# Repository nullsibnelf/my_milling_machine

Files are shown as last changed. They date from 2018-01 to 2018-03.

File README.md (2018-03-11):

# my_milling_machine
open source hardware - PCB-milling and engraving machine

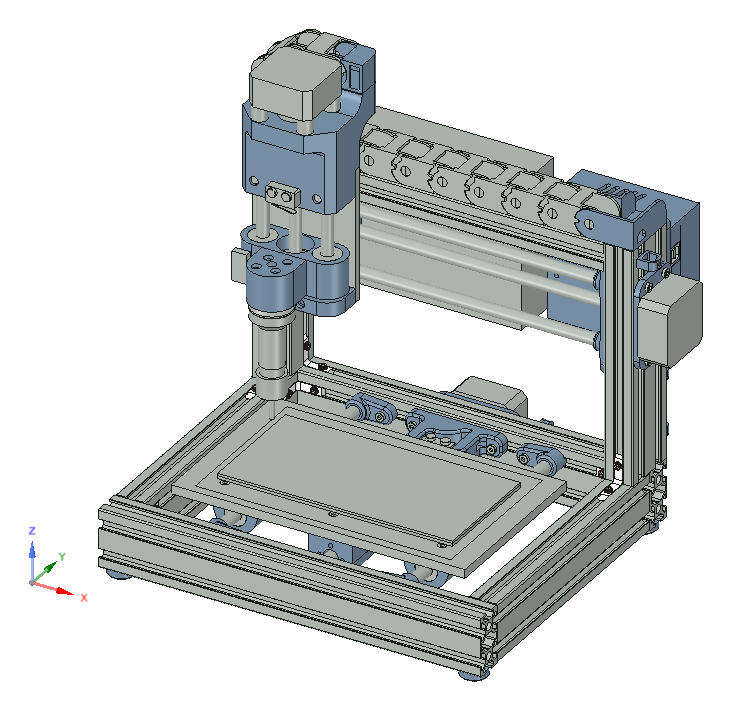
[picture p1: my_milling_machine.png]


Goal:
- low budget machine to make pcb's without expensive software
- little machine overall size, to fit in a cupboard
- open hardware to support further development

<p>&nbsp;</p>

Features:
- Size 310 x 260 x 280 mm
- working volume 173 x 108 x 35 mm
- standard 1/8" tool fitting
- Arduino based
- connection via USB or Bluetooth
- auto-homing

<p>&nbsp;</p>

Further Development:
- Tool referencing
- interchangeable toolhead for mounting a laser module too
- camera for optical calibration
- dust extraction [Link](https://github.com/nullsibnelf/cyclone_dust_absorber)
- emergency shutdown

<p>&nbsp;</p>

2018/02/26: Total costs by now -> ~237€ plus 3D-printed parts

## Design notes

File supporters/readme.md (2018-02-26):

This section is for all those they supported this project with ideas, work and goods.    

**Special Thanks to:**

<br><p>
  
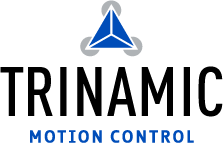
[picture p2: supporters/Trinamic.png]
    
  
**Trinamic**, for free testsamples of the <a href="https://www.trinamic.com/products/integrated-circuits/details/tmc2130/" target="_blank">TMC2130</a> for evaluation of my Arduino-CNC-HAT!    
Really great chip!    

<br><p>
  
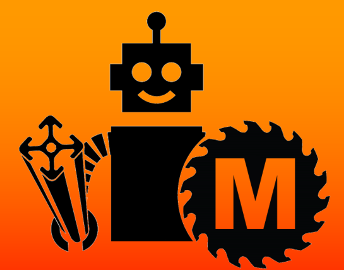
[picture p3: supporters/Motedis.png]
    
  
**Motedis**, for their great support and patience in mechanical qustions about the frame.    
Cheap parts at accurate and high quality! Get yours <a href="http://www.motedis.com/shop/">here!</a>

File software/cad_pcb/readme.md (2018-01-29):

folder for cad-files and the software Eagle from CADSoft.

<br>
<i>Eagle:</i>

All pcb-cad-files are made with Eagle.    
Download: http://ftp.cadsoft.de/freeware.htm
<p>&nbsp;<br></p>

<br>
<i>ULP Script pcb-gcode:</i>

To make gcode out of your board-file you need this ULP-script.    
Download: http://pcbgcode.org/list.php?12   

Changes: in file "settings/gcode-defaults.h" line 49 change    
```string SPINDLE_ON = "M03" + EOL + DWELL;```    
into    
```string SPINDLE_ON = "M03 S20" + EOL + DWELL;```

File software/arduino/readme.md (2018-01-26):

folder for arduino codes.
<p>&nbsp;</p>

<p>
<b>HC-05_config.ino:</b><br>    
This Sketch helps to configure the bluetooth module. You have to change the name, password and baudrate.<br>
Instruction how to do this can be found here: http://www.instructables.com/id/Modify-The-HC-05-Bluetooth-Module-Defaults-Using-A/
</p>
<p>&nbsp;</p>

<p>
<b>ESC_test.ino:</b><br>        
This Sketch was to test the ESC to run a brushless motor controlled by the arduino. Just for evaluation. Not needed.
</p>
<p>&nbsp;</p>

<p>
<b>GRBL:</b><br>     
My-milling-machine runs with GRBL firmware. It's a open source arduino based software that controlls the whole machine.<br>
Download: https://github.com/gnea/grbl/releases
</p>
<p>&nbsp;</p>

<p>
<b>GRBL ESC-patch:</b><br>       
My-milling-machine uses a brushless motor instead of an high-revolution cnc-spindle. GRBL doesn't support this by now. But there is a fork working, made by <a href="https://github.com/pablozg" target="new">pablozg</a>. Thanks for that!<br>
Download: https://github.com/gnea/grbl/pull/163/commits/012c7ed89ec174e6f918a2663bce6ed2ce5e7117
</p>
<p>&nbsp;</p>

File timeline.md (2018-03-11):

2018/01/29:    
All metal parts ordered. ETA 2-3 weeks.    

<br>

2018/02/13:    
Frame parts arrived today. Let's build it :-)

<br>

2018/02/22:    
ordered some wrong pieces. updated partlist accordingly. Waiting for the right parts now.

<br>

2018/03/11:    
Führung der Y-Achsen-Führung überarbeitet. Durch shrinking der 3D-Druckteile klemmten die Linearführungen leicht. Halter in 3 Teile gesplittet.    
Motoren für X und Y montiert und getestet. Verdrahtung und GRBL Konfiguration entsprechend angepasst.

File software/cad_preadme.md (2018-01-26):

folder for cad-files and the software Eagle from CADSoft.

<br>
All pcb-cad-files are made with Eagle.
Download: http://ftp.cadsoft.de/freeware.htm

<br>
To make gcode out of your board-file you need this ULP-script.
Download: http://pcbgcode.org/list.php?12

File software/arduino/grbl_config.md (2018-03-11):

Setting | Value | Beschreibung
--- | --- | --- 
$0   | 10 | 
$1   | 25 | 
$2   | 0 | 
$3   | 1 | Motor der X-Achse auf "Max"-Seite montiert
$4   | 0 | 
$5   | 0 | 
$6   | 0 | 
$10  | 1 | 
$11  | 0.010 | 
$12  | 0.002 | 
$13  | 0 | Maße in Millimeter
$20  | 1 | Softlimits aktiviert für Max-Position
$21  | 1 | Endschalter aktiviert für Homing
$22  | 1 | Homing freigeschaltet
$23  | 3 | Homing X + Y nach Null, Z nach Max
$24  | 25.000 | 
$25  | 500.000 | 
$26  | 250 | 
$27  | 2.000 | Verfahrweg für Freigabe der Endschalterin Millimetern
$30  | 1000 | 
$31  | 0 | 
$32  | 0 | 
$100 | 100.000 | Stepps pro Millimeter X-Achse
$101 | 100.000 | Stepps pro Millimeter Y-Achse
$102 | 100.000 | Stepps pro Millimeter Z-Achse
$110 | 500.000 | Max-Verfahrrate mm/min X-Achse
$111 | 500.000 | Max-Verfahrrate mm/min Y-Achse
$112 | 500.000 | Max-Verfahrrate mm/min Z-Achse
$120 | 10.000 | Beschleunigung mm/sec² X-Achse
$121 | 10.000 | Beschleunigung mm/sec² Y-Achse
$122 | 10.000 | Beschleunigung mm/sec² Z-Achse
$130 | 175.000 | Max-Weg X-Achse (173 + 2mm für Endtaster)
$131 | 110.000 | Max-Weg Y-Achse (108 + 2mm für Endtaster)
$132 | 38.000 | Max-Weg Z-Achse (36 + 2mm für Endtaster)

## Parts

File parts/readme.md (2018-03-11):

folder for parts you need to build my_milling_machine
<p>&nbsp;</p>

**Machine parts:**

Part | Price | Link | Tested
--- | --- | --- | ---
Arduino Uno clone | 3,41 € | <a href="https://www.banggood.com/UNO-R3-ATmega328P-Development-Board-For-Arduino-No-Cable-p-964163.html" target="_blank">Link</a> | checked
HC-05 bluetooth module | 3,66 € | <a href="https://www.banggood.com/de/3Pcs-HC-05-Wireless-Bluetooth-Serial-Transceiver-Module-For-Arduino-p-1011725.html" target="_blank">Link</a> | checked
Stepper motor driver (3x) | 32,85 € | <a href="http://www.watterott.com/de/SilentStepStick-TMC2130" target="_blank">Link</a> | checked
ESC for spindle | 15,66 € | <a href="https://www.amazon.de/gp/product/B07661T5N2/ref=oh_aui_detailpage_o00_s02?ie=UTF8&psc=1" target="_blank">Link</a> | checked
Brushless motor | 7,50 € | <a href="https://www.amazon.de/LHI-MT2204%E2%85%A1-Brushless-Quadcopter-Multicopter/dp/B01E3OT7NE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" target="_blank">Link</a> | checked
5mm ER11 spindle | 4,02 € | <a href="https://www.banggood.com/ER11A-5mm-Extension-Rod-Holder-Motor-Shaft-Collet-Chuck-Tool-Holder-CNC-Milling-p-1073852.html" target="_blank">Link</a> | checked
1/8" ER11 clamp | 0,82 € | <a href="https://www.banggood.com/ER11-18-Inch-Spring-Collet-for-CNC-Milling-Lathe-Tool-p-1080679.html" target="_blank">Link</a> | checked
Trapezoidal threaded rod with carrier and bearings (3x) | 38,94 € | <a href="https://www.amazon.de/gp/product/B06Y583KK4/ref=ox_sc_act_title_2?smid=AK9FVUO3F9GPF&psc=1" target="_blank">Link</a> | under investigation
Slide bearing (8x) | 12,00 € | <a href="https://www.amazon.de/gp/product/B06WD7M4ZJ/ref=ox_sc_act_title_3?smid=A2LZ0UUKEAXYKL&psc=1" target="_blank">Link</a> | checked
Power supply 100W 12V & 5V | 10,63 € | <a href="https://www.banggood.com/5V12V24V-Power-Supply-Box-For-large-Game-Consoles-p-1120203.html" target="_blank">Link</a> | under investigation
Nema17 stepper motor short (3x) | 30,99 € | <a href="https://www.amazon.de/Beauty-Star-Schrittmotor-Haltemomentf%C3%BCr-Halterung/dp/B07784Y8ML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" target="_blank">Link</a> | checked
End switch (3x) | 0,59 € | <a href="https://www.amazon.de/gp/product/B00U8MPFLO/ref=oh_aui_search_detailpage?ie=UTF8&psc=1" target="_blank">Link</a> | checked
Supply cable 230V (or equivalent) | tbd | n/a |
wiring cables | tbd | n/a |
PE cables | tbd | n/a |
CNC-shield for Arduino | self made | [Link](https://github.com/nullsibnelf/my_milling_machine/tree/master/parts/arduino_shield) | under redesign
Coolingfan for step-drivers on CNC-shield | tbd | n/a |
Reset / emergency-Stop switch | tbd | n/a |
&nbsp; | 161,07 € | |
<p>&nbsp;</p>

**Frame parts:**

Part | Price | Link | Comment
--- | --- | --- | ---
Profile 20x40 B-Typ Nut 6 | 10,89 € |	<a href="http://www.motedis.com/shop/Nutprofil/20-B-Typ-Nut-6/Aluprofil-20x40-B-Typ-Nut-6::158.html" target="_blank">Link</a>
Precision guide bar 8mm Alu (6x + rest) | 15,23 € |	<a href="http://www.motedis.com/shop/Dynamik-Lineareinheiten/Praezisionswellen/Alu-Praezisionswellen-Zuschnitt/Praezisionswelle-Aluminium-%D88mm::3501.html" target="_blank">Link</a>
Machine table 6mm Alu (200x120) |	6,56 € |	<a href="http://www.motedis.com/shop/Halbzeuge/Aluminium-Plaettchen/Aluminium-Plaettchen-beidseitig-feinstgefraest-und-foliert-Plaettchen-Zuschnitt/Plaettchen-Zuschnitt/Alumi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" target="_blank">Link</a>
Spindle mounting plate 6mm Alu (80x64) |	1,39 € |	<a href="http://www.motedis.com/shop/Halbzeuge/Aluminium-Plaettchen/Aluminium-Plaettchen-beidseitig-feinstgefraest-und-foliert-Plaettchen-Zuschnitt/Plaettchen-Zuschnitt/Alumi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" target="_blank">Link</a>
Energy chain links (12x) |	4,86 € |	<a href="http://www.motedis.com/shop/Energiekette/Energiekette/Energiekette-CK15/Energiekette-CK-15-Breite-15mm-einzelne-Glieder::2948.html" target="_blank">Link</a>
Energy chain tail (2x) |	2,69 € |	<a href="http://www.motedis.com/shop/Energiekette/Energiekette/Energiekette-CK15/Energiekette-CK-15-Breite-15mm-Anschlusselemente-1-Paar::2946.html" target="_blank">Link</a>
Profile Nut M3 (30x) |  	6,72 € | <a href="http://www.motedis.com/shop/Nutprofil-Zubehoer/Zubehoer-20-B-Typ-Nut-6/Hammermutter-B-Typ-Nut-6-M3::4752.html" target="_blank">Link</a>
Profile Joint (16x) | 		14,63 € | <a href="http://www.motedis.com/shop/Nutprofil-Zubehoer/Zubehoer-20-B-Typ-Nut-6/Innenwinkel-Stahl-20-B-Typ-Nut-6-099I90R06::565.html" target="_blank">Link</a>
shipping |	11,90 € |
&nbsp; |	74,87 € |	
 
<p>&nbsp;</p>

**Commodities:**

Part | Price | Link | Tested
--- | --- | --- | ---
FR4 CU | 11,96 € | <a href="https://www.banggood.com/10Pcs-1_5MM-CCL-1015-FR4-Glass-Fiber-Board-PCB-Circuit-Board-p-962233.html" target="_blank">Link</a> |
Wooden support | tbd | n/a | 
Contour router 0.1mm (5x) | 3,70 € | <a href="https://www.banggood.com/5pcs-0_1mm-15-Degree-Titanium-Coated-Carbide-Flat-Bottom-PCB-Engraving-Bit-CNC-Router-Tool-p-1034790.html" target="_blank">Link</a> |
End mill cutter mix (10x) | 3,63 € | <a href="https://www.banggood.com/10pcs-11_522_53mm-Carbide-End-Mill-Cutter-PCB-Drill-Bits-p-1090388.html" target="_blank">Link</a> | 
Drill 1mm (10x) | 3,63 € | <a href="https://www.banggood.com/10pcs-1_0mm-Mini-PCB-Drill-Bits-Tungsten-Steel-For-CNC-Print-Circuit-Board-p-995198.html" target="_blank">Link</a> |
<p>&nbsp;</p>

**Printed parts:**

tbd. All blue parts in the 3D model.

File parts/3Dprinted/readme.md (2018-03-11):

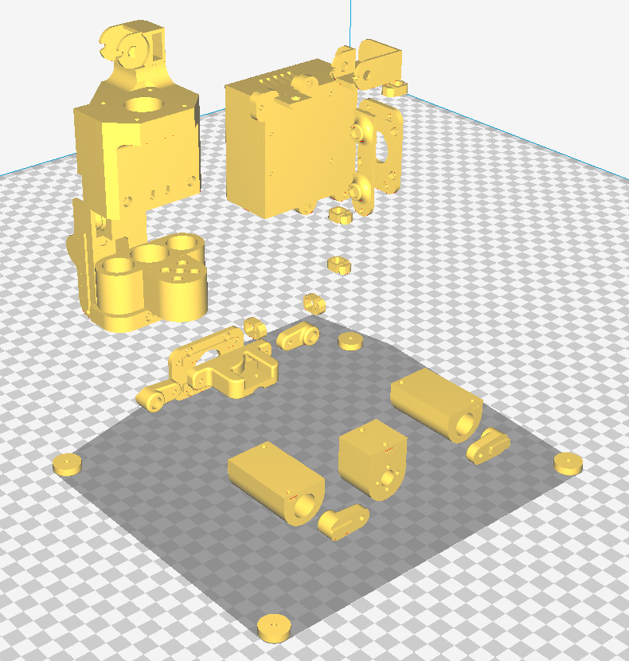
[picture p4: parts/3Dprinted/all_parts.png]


Für diese Projekt müssen einige Teile 3D-gedruckt werden.   
Laut Slicer (Cura) beläuft sich der Filamentbedarf auf ~250gr (ohne Support)

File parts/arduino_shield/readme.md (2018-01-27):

folder for the files related to the customized arduino CNC-shield
<p>&nbsp;</p>

- It is designed to fit on an Arduino Uno.    
- As stepper drivers I've chosen watterott's TMC2130 board. The board supports 3 Axis: X, Y and Z.    
- For better connectivity I added a HC-05 bluetooth-module. Baudrate stays at 115.200.    
- To avoid trouble while flashing (because of the HC-05 is parallel), the bluetooth module is powered by an Arduino-Port.
- The shield has 2 supply inputs: 5V for logic and the Arduino-board, and 12V for the steppers and the ESC/brushless motor.    
<p>&nbsp;</p>

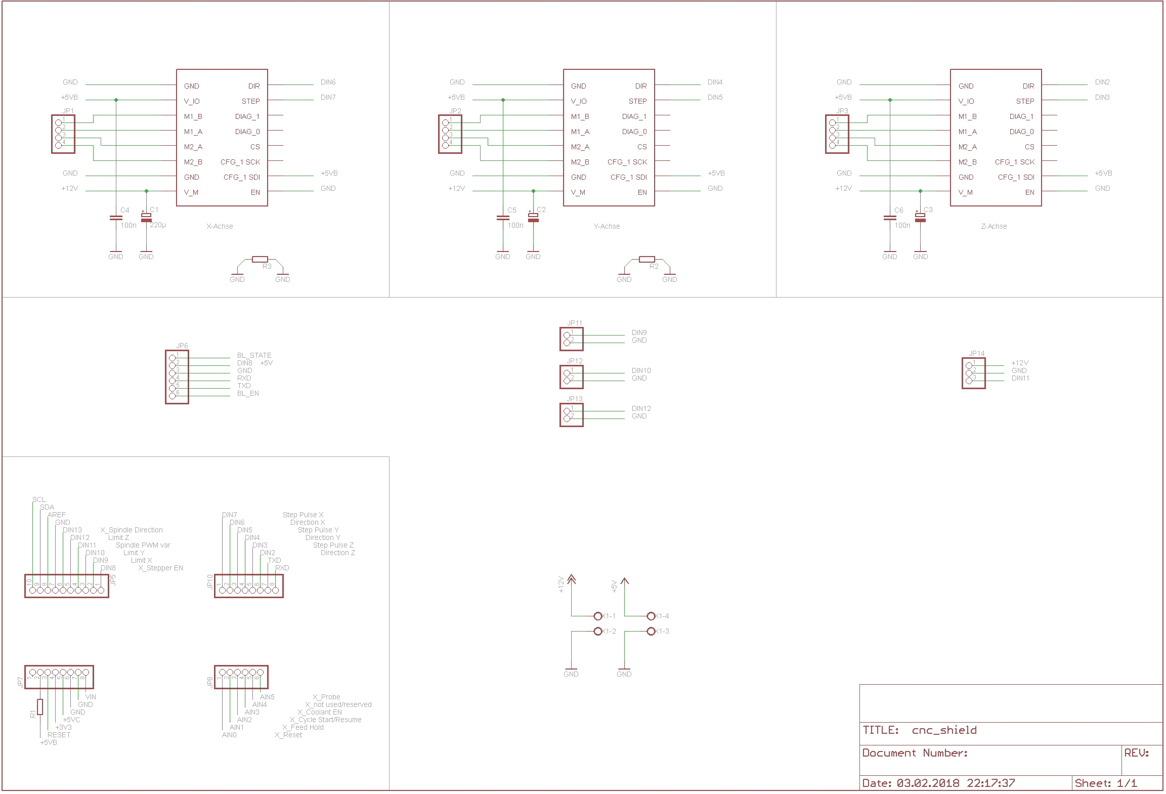
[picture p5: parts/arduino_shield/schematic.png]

<p>&nbsp;</p>

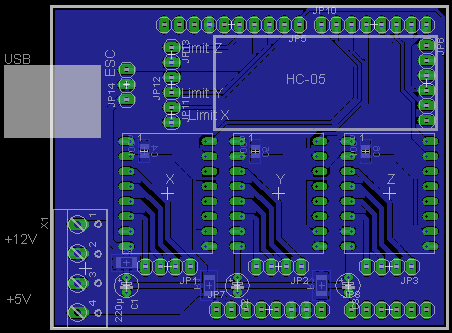
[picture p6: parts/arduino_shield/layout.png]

<p>&nbsp;</p>

<table>
    <tr>
        <td> new </td>
        <td> grbl </td>
        <td> pin </td>
        <td> port </td>
        <td> &nbsp </td>
        <td> port </td>
        <td> pin </td>
        <td> grbl </td>
        <td> new </td>
    </tr>
    <tr></tr>
    <tr>
        <td>   </td>
        <td>   </td>
        <td>   </td>
        <td>   </td>
        <td>   </td>
        <td>   </td>
        <td> SCL </td>
        <td>   </td>
        <td>   </td>
    </tr>
    <tr>
        <td>   </td>
        <td>   </td>
        <td>   </td>
        <td>   </td>
        <td>   </td>
        <td>   </td>
        <td> SDA </td>
        <td>   </td>
        <td>   </td>
    </tr>
    <tr>
        <td>   </td>
        <td>   </td>
        <td>   </td>
        <td>   </td>
        <td>   </td>
        <td>   </td>
        <td> AREF </td>
        <td>   </td>
        <td>   </td>
    </tr>
    <tr>
        <td>   </td>
        <td>   </td>
        <td>   </td>
        <td>   </td>
        <td>   </td>
        <td>   </td>
        <td> GND </td>
        <td>   </td>
        <td>   </td>
    </tr>
    <tr>
        <td>   </td>
        <td>   </td>
        <td>   </td>
        <td>   </td>
        <td>   </td>
        <td>   </td>
        <td> Dig_13 </td>
        <td> Spindle direction  </td>
        <td>   </td>
    </tr>
    <tr>
        <td> 5V </td>
        <td> 5V </td>
        <td> 5V </td>
        <td>   </td>
        <td>   </td>
        <td>   </td>
        <td> Dig_12 </td>
        <td> Limit Z </td>
        <td> Limit switch Z </td>
    </tr>
    <tr>
        <td>  </td>
        <td>  </td>
        <td> Reset </td>
        <td>   </td>
        <td>   </td>
        <td>   </td>
        <td> Dig_11 </td>
        <td> Variable Spindle PWM </td>
        <td> ESC PWM </td>
    </tr>
    <tr>
        <td>  </td>
        <td>  </td>
        <td> 3V3 </td>
        <td>   </td>
        <td>   </td>
        <td>   </td>
        <td> Dig_10 </td>
        <td> Limit Y </td>
        <td> Limit switch Y </td>
    </tr>
    <tr>
        <td>  </td>
        <td>  </td>
        <td> 5V </td>
        <td>   </td>
        <td>   </td>
        <td>   </td>
        <td> Dig_09 </td>
        <td> Limit X </td>
        <td> Limit switch X </td>
    </tr>
    <tr>
        <td>  </td>
        <td>  </td>
        <td> GND </td>
        <td>   </td>
        <td>   </td>
        <td>   </td>
        <td> Dig_08 </td>
        <td> Stepper enable </td>
        <td> Bluetooth module 5V </td>
    </tr>
    <tr>
        <td>  </td>
        <td>  </td>
        <td> GND </td>
        <td>   </td>
        <td>   </td>
        <td>   </td>
        <td>  </td>
        <td>  </td>
        <td>  </td>
    </tr>
    <tr>
        <td>  </td>
        <td> VIN </td>
        <td>  </td>
        <td>   </td>
        <td>   </td>
        <td>   </td>
        <td> Dig_07 </td>
        <td> Z Direction </td>
        <td> Z Direction </td>
    </tr>
    <tr>
        <td>  </td>
        <td>  </td>
        <td>  </td>
        <td>   </td>
        <td>   </td>
        <td>   </td>
        <td> Dig_06 </td>
        <td> Y Direction </td>
        <td> Z Step </td>
    </tr>
    <tr>
        <td>  </td>
        <td> Reset / Abort </td>
        <td> Analog_0 </td>
        <td>   </td>
        <td>   </td>
        <td>   </td>
        <td> Dig_05 </td>
        <td> X Direction </td>
        <td> Y Direction </td>
    </tr>
    <tr>
        <td>  </td>
        <td> Feed Hold </td>
        <td> Analog_1 </td>
        <td>   </td>
        <td>   </td>
        <td>   </td>
        <td> Dig_04 </td>
        <td> Z Step </td>
        <td> Y Step </td>
    </tr>
    <tr>
        <td>  </td>
        <td> Cycle Start / Resume </td>
        <td> Analog_2 </td>
        <td>   </td>
        <td>   </td>
        <td>   </td>
        <td> Dig_03 </td>
        <td> Y Step </td>
        <td> X Direction </td>
    </tr>
    <tr>
        <td>  </td>
        <td> Coolant Enable </td>
        <td> Analog_3 </td>
        <td>   </td>
        <td>   </td>
        <td>   </td>
        <td> Dig_02 </td>
        <td> X Step </td>
        <td> X Step </td>
    </tr>
    <tr>
        <td>  </td>
        <td> reserved </td>
        <td> Analog_4 </td>
        <td>   </td>
        <td>   </td>
        <td>   </td>
        <td> TxD </td>
        <td>  </td>
        <td> Bluetooth module Rx </td>
    </tr>
    <tr>
        <td>  </td>
        <td> Probe </td>
        <td> Analog_5 </td>
        <td>   </td>
        <td>   </td>
        <td>   </td>
        <td> RxD </td>
        <td>  </td>
        <td> Bluetooth module Tx </td>
    </tr>
</table>
<p>&nbsp;</p>

Further changes:<br>
- dust absorbtion
- ws2812 for printhead lightning
- Z probing
- emergency shutoff
- endstop via stall-detection within TMC2130

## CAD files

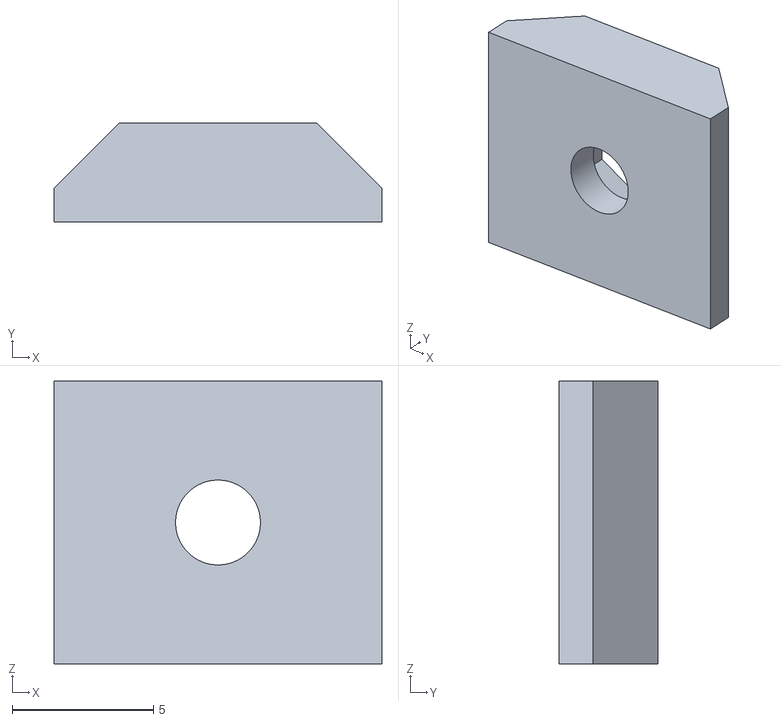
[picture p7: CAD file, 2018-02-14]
parts/3Dprinted/nutstein m2_5.stl
11.6 x 3.50 x 10.0

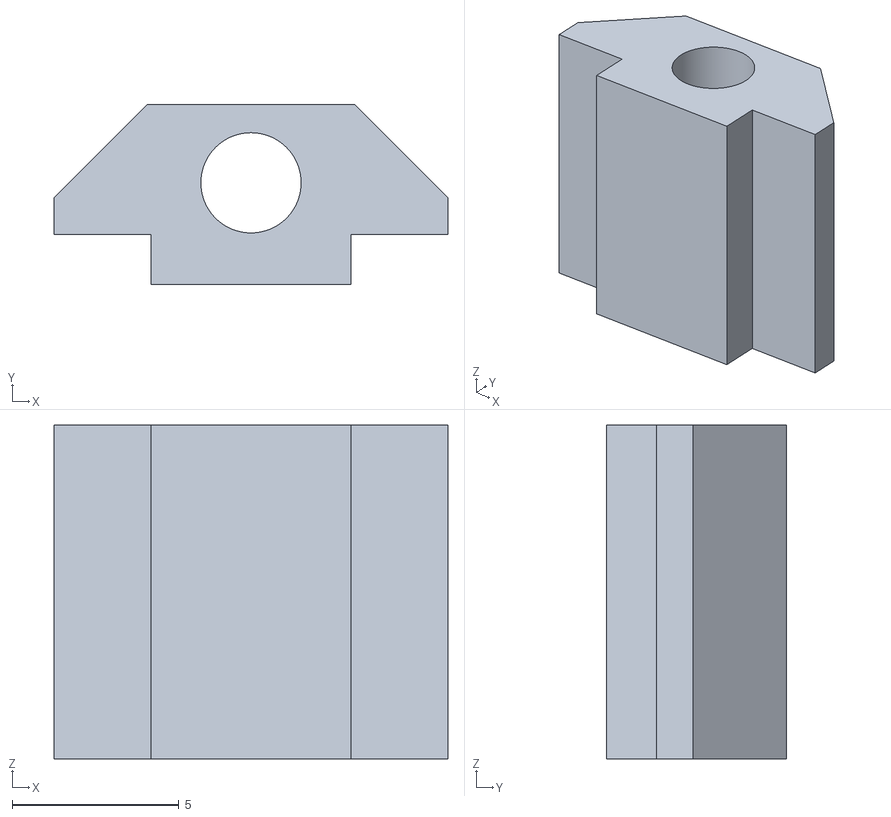
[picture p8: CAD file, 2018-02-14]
parts/3Dprinted/verbinder m2_5.stl
11.8 x 5.40 x 10.0

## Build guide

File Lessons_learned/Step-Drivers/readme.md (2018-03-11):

**Thermisches Verhaltender Stepper-driver:**   
Die Treiberbausteine werden recht warm, da die Motoren wegen der mangelnden selbsthaltung dauerbestromt werden müssen. Kühlkörper sind zwingend erforderlich. Zusätzlich sollte ein Lüfter verbaut werden, um die Kühlrippen zu entwärmen. Bei thermischer Notabschaltung des IC's drohen Schrittverluste.    

&nbsp;
<br>

**Selbstdesignte PCB mit integrierten Stepper-drivern:**    
Leider musste ich den Plan der fest verlöteten Bausteine aufgeben, da von hand keine korrekte Lötung des I-Pads möglich ist. Ziel war Platz zu sparen und die entwärmung zu optimieren. Es wird wohl weiter mit den "Silent Step-Sticks" gearbeitet werden müssen.

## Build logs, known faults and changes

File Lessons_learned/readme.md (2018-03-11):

please refer to the detailed description of each problem.

- Load Dump
- Stepper-driver

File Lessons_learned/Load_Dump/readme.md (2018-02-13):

Failure:    
ESC from dustabsorber from 50% max revolution to zero via commandline (M3, delay, M5). 
Arduino supplied via Vin-Pin from CNC-Shield (12V)    
<br>

Consequence:    
12V Line raised zu 36V (maybe more, 36V on the display of the powersupply) and burned the Arduino LD1117-5V-IC. Plus all 3 stepper drivers :-/    
<br>

Reflief:
Variant A - go step by step from v-max to zero by incdreasing in 5% steps per 100ms. !Don't know if possible in G-Code!
Variant B - splitting the Supply in 2 Lines (Powersupply with 5V and 12V path, like ATX)
Variant C - adding load-Dump diodes, PI-filters, z-diodes ect. in layout on high current paths and logic parts    

<br>

Solved with suppressor-diode SM6HT-27.

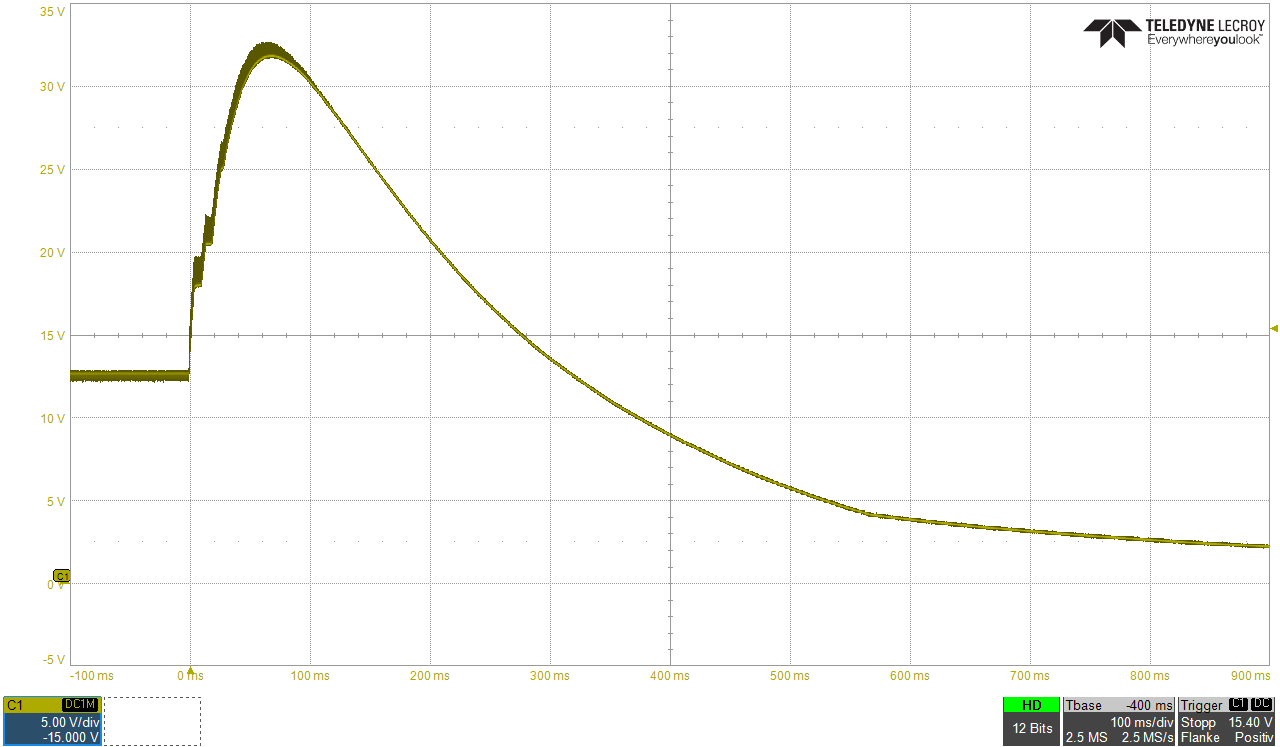
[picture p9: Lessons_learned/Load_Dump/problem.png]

This pulse is generated by the ESC during motor-stop. The pulse would be higher, but at 32V the power-supply went in OVP (overvoltage protection) and cut off the supply.    
<br>

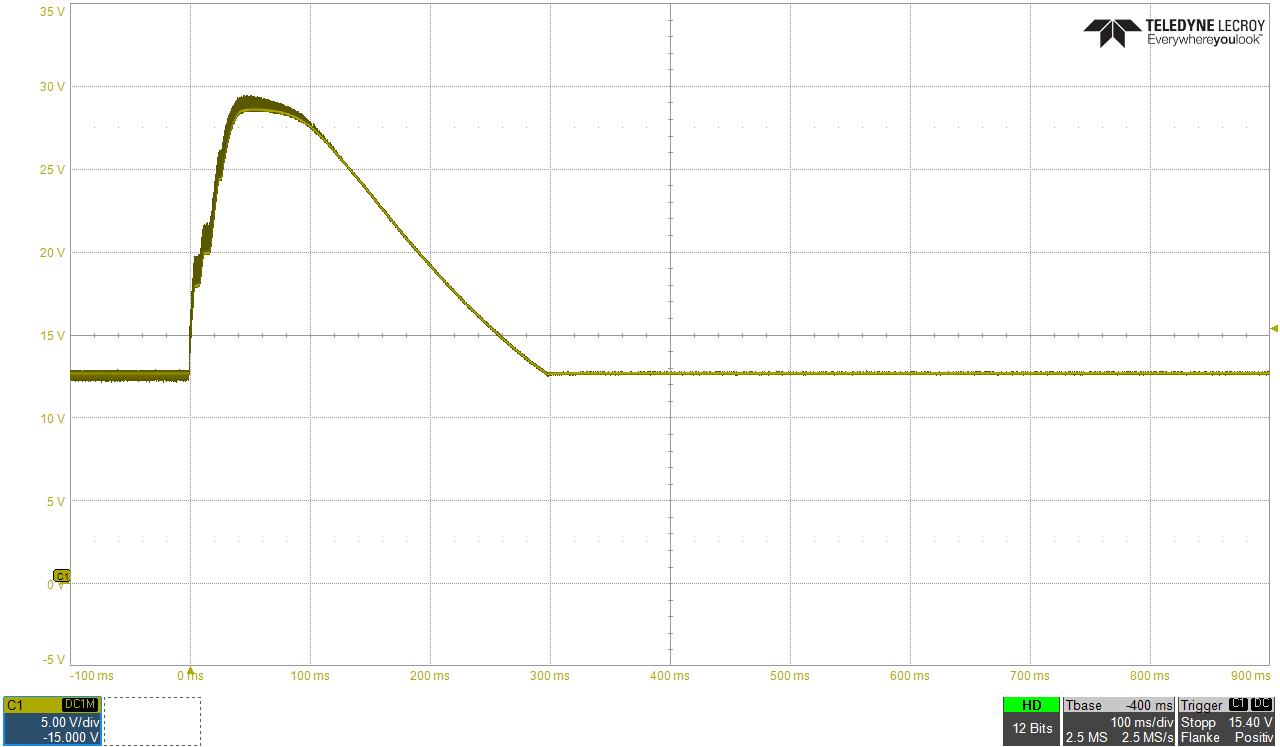
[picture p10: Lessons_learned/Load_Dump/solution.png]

With a supressor-diode parallel to the supply of the ESC the pulse is cutted at a level of 27V. The energy above is consumed by the diode. No OVP occures.    

Detailed info here: <a href="https://en.wikipedia.org/wiki/Transient-voltage-suppression_diode">Wikipedia</a>

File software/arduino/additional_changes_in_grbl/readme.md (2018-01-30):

all additional SW changes in GRBL after "ESC-patch".

cpu_map.h:    
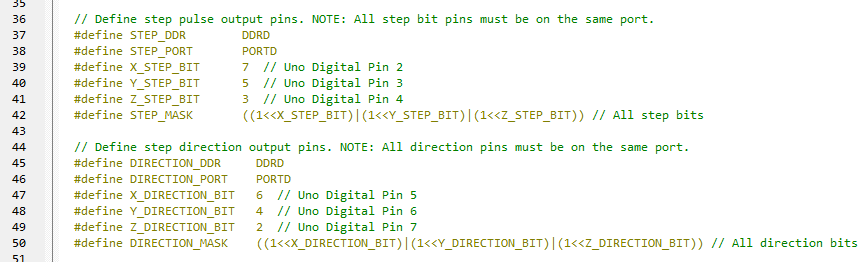
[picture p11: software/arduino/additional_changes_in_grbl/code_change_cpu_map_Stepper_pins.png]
      
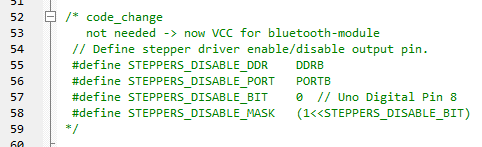
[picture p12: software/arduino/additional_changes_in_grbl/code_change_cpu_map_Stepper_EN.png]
1b
      

main.h:    
    

config.h:    
    

stepper.h:    
    

    



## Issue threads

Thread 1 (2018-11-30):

Aktueller Stand des Projekts

Mad-Onion, 2018-11-30:
Hallo Steffen,

ich bin durch Zufall auf dieses für mich total interessante Projekt gestoßen. Entwickelst du es noch aktiv weiter? Wie ist der aktuelle Stand? :-)

Beste Grüße
Tobias

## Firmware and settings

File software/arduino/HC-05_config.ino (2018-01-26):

/*

AUTHOR: Hazim Bitar (techbitar)
DATE: Aug 29, 2013
LICENSE: Public domain (use at your own risk)
CONTACT: techbitar at gmail dot com (techbitar.com)

*/


#include <SoftwareSerial.h>

SoftwareSerial BTSerial(10, 11); // RX | TX

void setup()
{
  pinMode(9, OUTPUT);  // this pin will pull the HC-05 pin 34 (key pin) HIGH to switch module to AT mode
  digitalWrite(9, HIGH);
  Serial.begin(9600);
  Serial.println("Enter AT commands:");
  BTSerial.begin(38400);  // HC-05 default speed in AT command more
}

void loop()
{

  // Keep reading from HC-05 and send to Arduino Serial Monitor
  if (BTSerial.available())
    Serial.write(BTSerial.read());

  // Keep reading from Arduino Serial Monitor and send to HC-05
  if (Serial.available())
    BTSerial.write(Serial.read());
}

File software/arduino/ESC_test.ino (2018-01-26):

#include <Servo.h>

#define Taster           9
#define StatusLed       13

Servo esc;


void setup() 
{
  pinMode(StatusLed,   OUTPUT);
  pinMode(Taster,      INPUT_PULLUP);
  
  Serial.begin(9600);                         // setup serial for debugging

  esc.attach(11);
  esc.writeMicroseconds(1000);
}




void loop()
{



  if (digitalRead(Taster) == 0)
  {
    Serial.println("T1");  
    
  int val;
  val = 400;
  val = map(val, 0, 1023, 1000, 2000);
  esc.writeMicroseconds(val);

    
    while (digitalRead(Taster) == 0);
  }

}

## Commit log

2018-01-26 Link to the ESC patch
2018-01-27 adding Pin-Table
2018-01-29 last fixes for the frame.
    Design Freeze for the frame. parts ordered
2018-02-09 updated cutter, spindle, powersupply
2018-02-16 update of table bearings
